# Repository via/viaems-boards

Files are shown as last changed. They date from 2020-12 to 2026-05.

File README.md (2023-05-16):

# viaems-boards
ViaEMS PCB Designs

In order of creation...
## Analog V1
 - Analog/ADC Core board based on a DIP TLC2543
 - All throughhole
 - Dedicated 5V supply
 - 4 Thermistor inputs
 - Inputs for EGO, BRV, MAP, TPS
 - 5 Spares

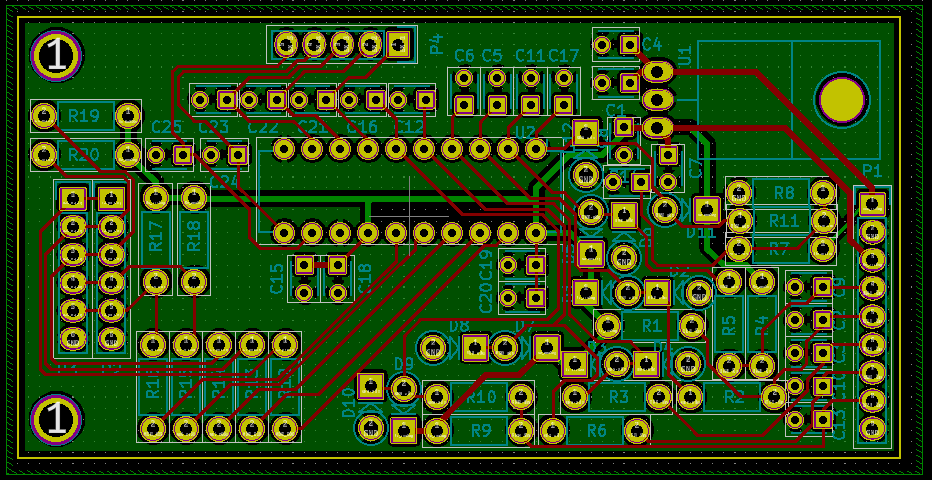
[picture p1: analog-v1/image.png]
 

## IO V1
 - IO core board
 - 4x ignition outputs
 - 6x Low side drivers
 - CAN driver
 - Digital inputs

Do not use because:
 - 3v supply for CAN doesn't work at all
 - the FETs without gate drivers has poor performance from a 3.3 V
   microcontroller
 - No VR inputs

## Viaems V1
Original all-in-one board for ViaEMS
 - STM32F407VGT
 - 8x Low side outputs (fed by gate drivers)
 - 4x ignition outputs
 - 2x High side drivers
 - Dedicated MAP and AAP sensors on-board
 - AD7888 SPI ADC with thermistor and core inputs, one spare
 - CAN driver

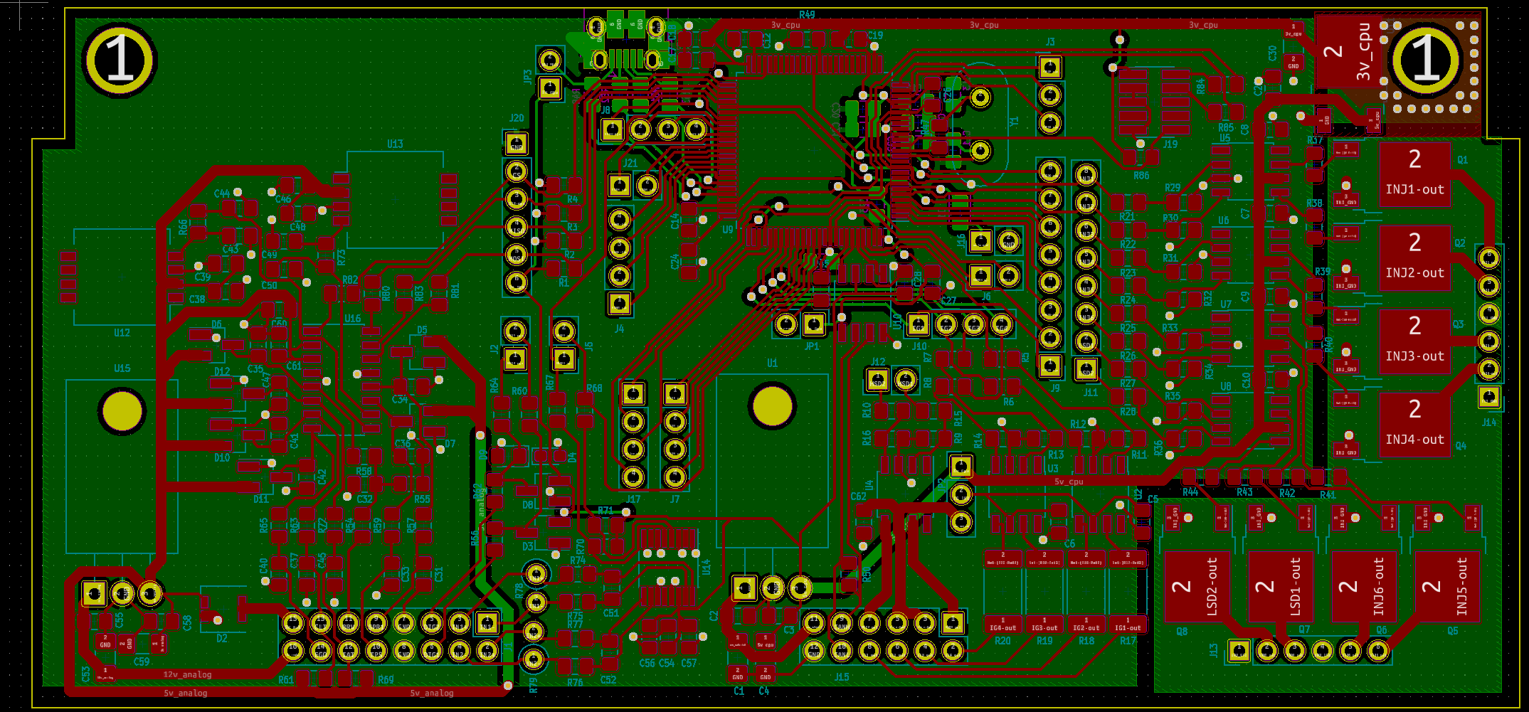
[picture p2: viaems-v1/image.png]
 

Shouldn't be used anymore, but really only because the outputs chosen for test
trigger vs real triggers are different in firmware.  The board can be used
again with some minor tweaks (and I have used this board for years)

## Analog V2
Experiment board to prototype use of the MAX11632, and some knock sensing
equipment.  The ADC samples fast enough to dedicate two inputs to knock sensing,
which uses an op amp input filter.  Provides core inputs, a dedicated MAP
sensor, and an additional 8 spare inputs.

The board works fine, but I'm unlikely to commit to the MAX11632: since it seems
incredibly finicky with SPI noise, and it doesn't provide a good way to know if
there is an issue. It requires a setup command.  The knock sensing filter works
great though.  Ultimately issues with this chip pushed me to investigate the
TLV2553.

Also, its way too big.

## IO V2
** Do not use! **
Simple breakout board as an upgrade to IO V2:
 - IO Core board
 - 5v supply (and fused output)
 - 4x ignition outputs
 - 8x Low Side drivers (including 4 injectors)
 - 2x Digital inputs
 - 2 VR inputs

Experiment with replacing the 2-port gate drivers with the 4-port MIC4469
 variant.  This board was made mostly to experiment with various FETs.

This board is missing inline resistors between the MIC4469 and FETs.  This is
incredibly important for the VND7NV04 -- without it, the negative pulse from
injectors destroys the gate control logic and causes it to latch partly on.

Ultimately this board is also *way* too big.

## Analog V3
Another experiment, this time for the TI TLV2553.  This ADC has only 11 inputs,
and samples at 200kHz (vs 300 kHz of the MAX11632).  However, its control is
identical to the TLC2543, which has self test functionality.  It is still fast
enough to allow for two inputs to be sampled at 40 kHz (and the rest at 10 kHz).
 - Analog Core board based on TLV2553
 - Small form factor (78x34 mm)
 - 2x SPI headers to make debugging easier
 - dedicated 5v supply (and fused output)
 - 1x MAP input
 - 2x knock sensor inputs
 - 3x Spare inputs

 I decided (after the fact) to make all the other boards the same form factor

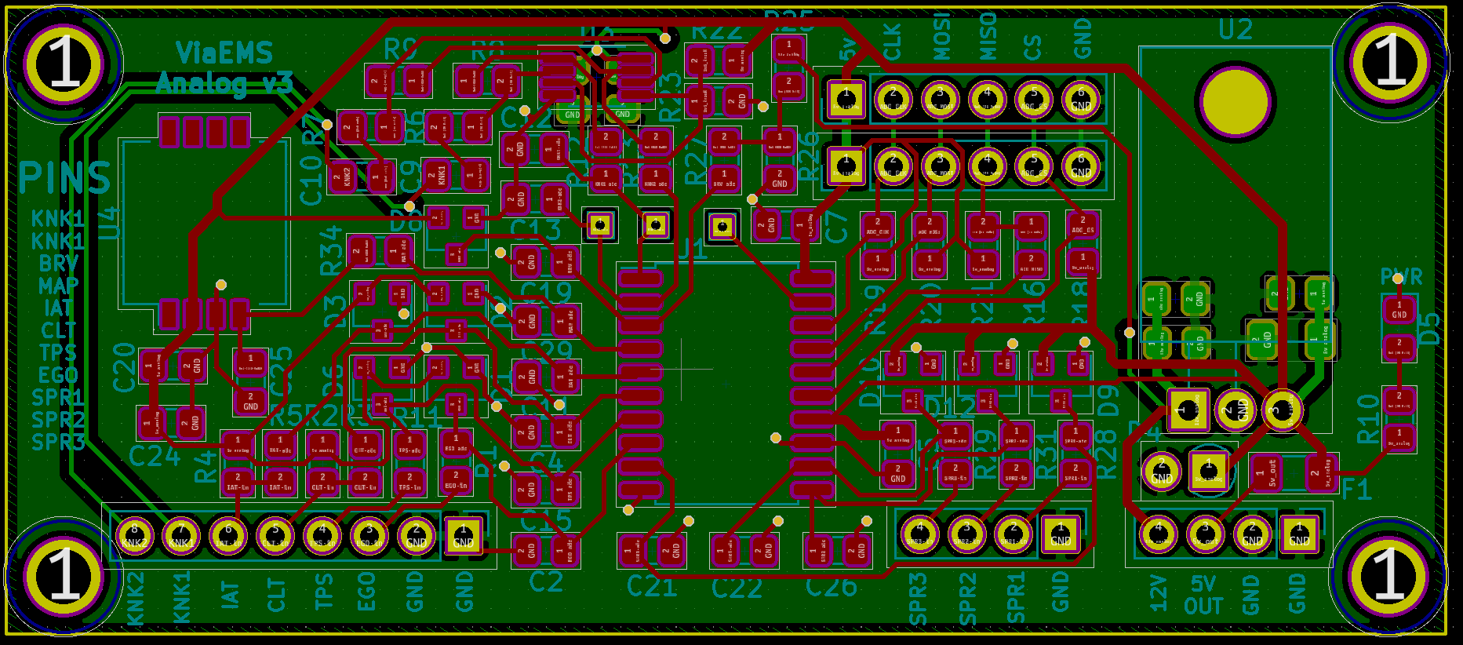
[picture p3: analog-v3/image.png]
 

## LSD V1 (Split from IO V2)
The full contents of IO V2 could not fit on a single 78x34 board, so it is split
into two -- one for the low side drivers, one for everything else.  Other
lessons learned from IO V2 were to add gate resistors for the FETs, and that
indicator LEDs are worth the effort to plan into the design.
 - Low side/Injector Core board
 - Small form factor (78x34)
 - 4x Injector outputs
 - 4x LSD outputs (or an extra 4x injectors)
 - Indicator LEDs

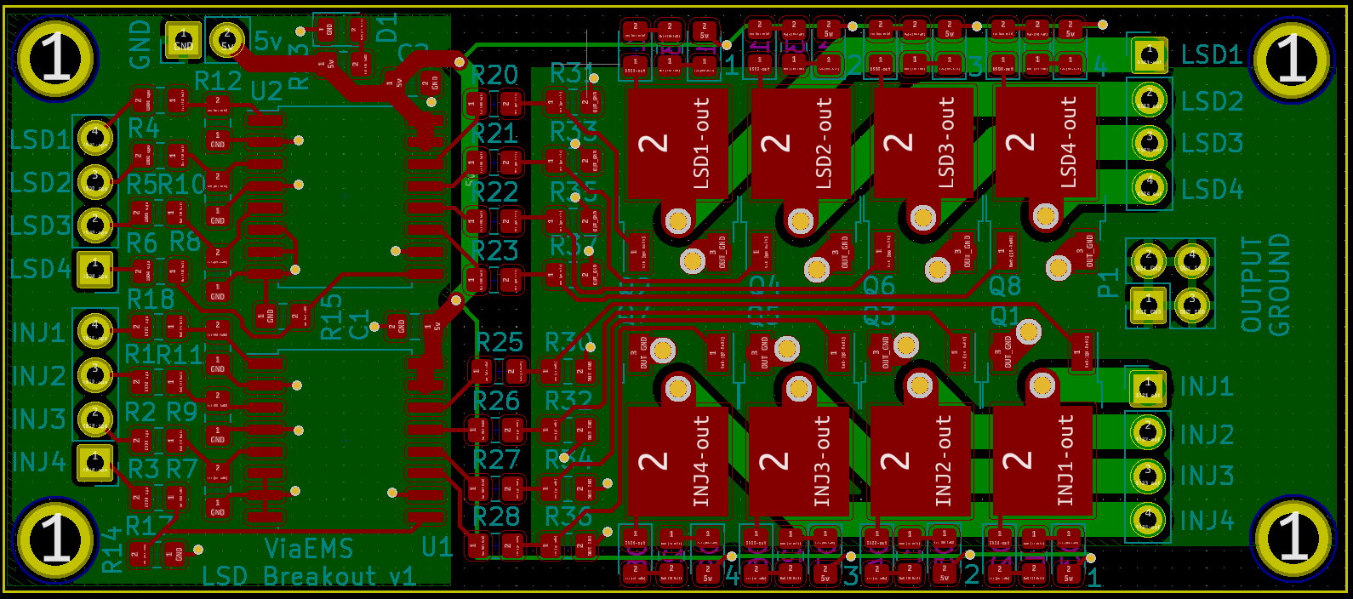
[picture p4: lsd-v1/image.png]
 

## Pwr-Ign-V1 (Split from IO V2)
An upgrade from IO V2, with gate resistors fixed, indicator LEDs on all outputs
and trigger inputs
 - 5v supply
 - 2x VR inputs
 - 2x Digital inputs
 - 4x Ignition outputs

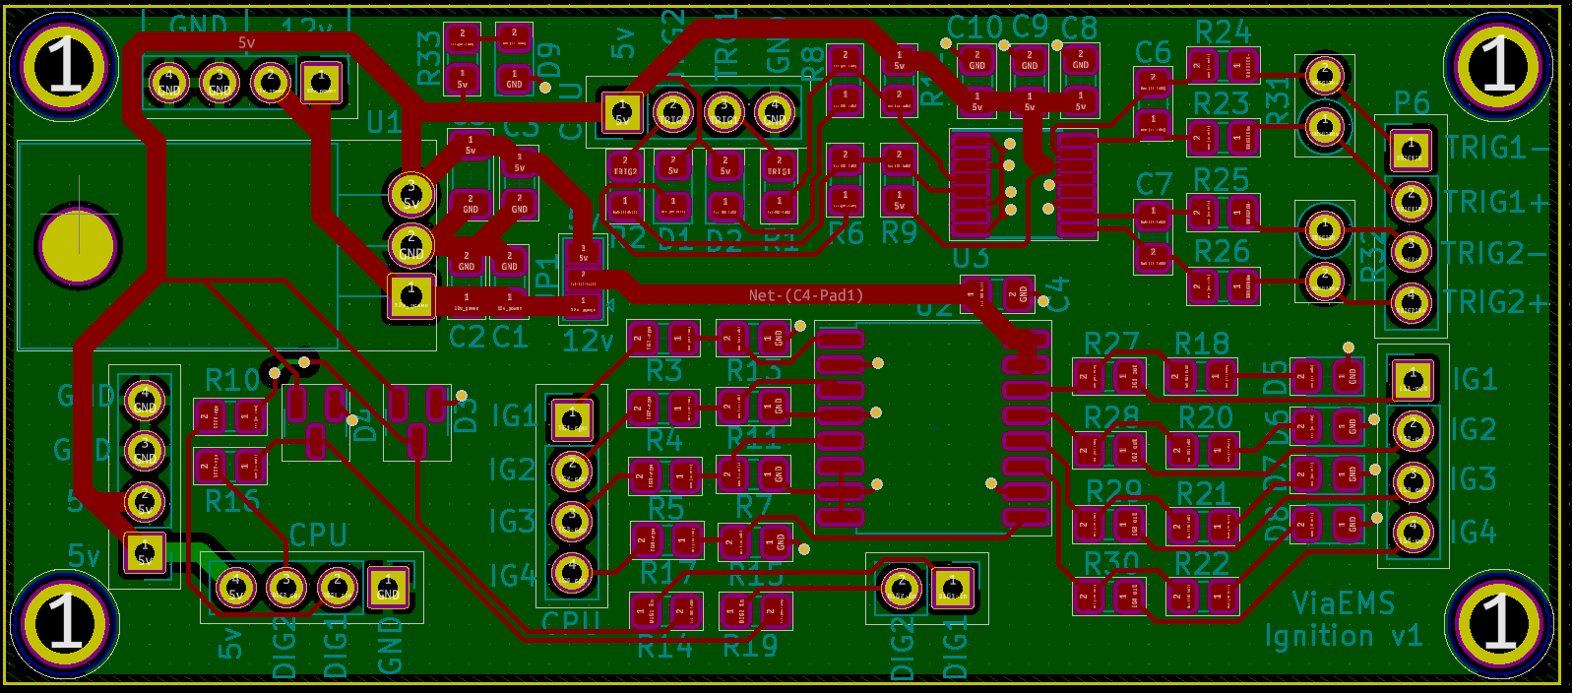
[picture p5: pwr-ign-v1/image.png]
 

## Proto-stm32f427 (v2)
Generic testing board for stm32f427 or gd32f470.  This is the same pcb
dimensions as the prior 3 boards, and comes with:
 - 100 LQFP footprint for microcontroller
 - USB Type-C (with FS-only pinout)
 - Optional soic-8 spi nor flash footprint on SPI1
 - Full 20 pin SWD+ETM trace connector

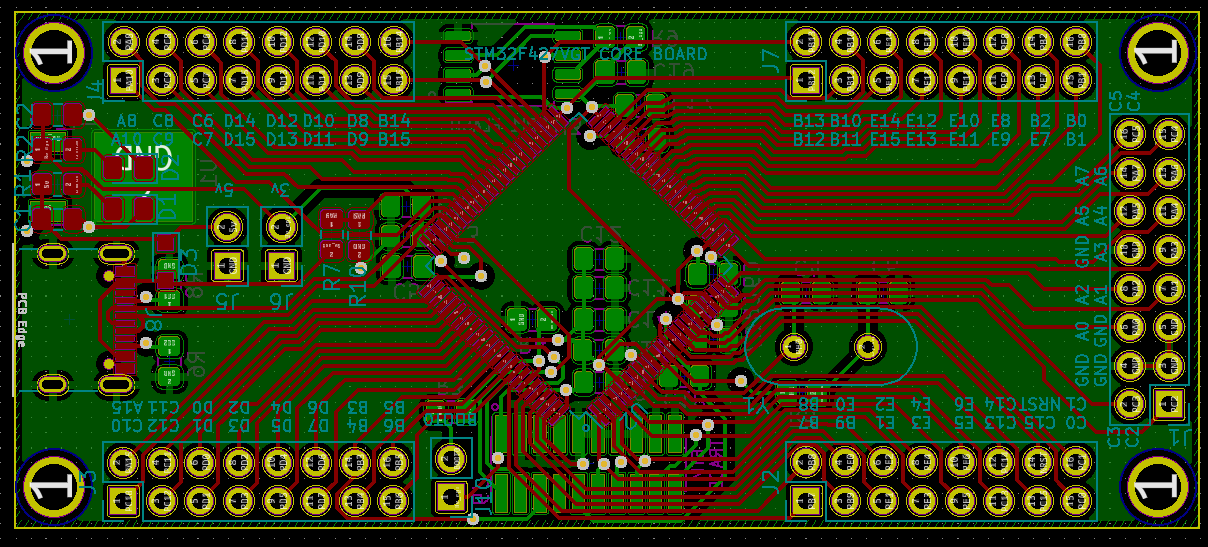
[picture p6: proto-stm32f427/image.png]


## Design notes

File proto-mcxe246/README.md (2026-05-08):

Power schemes:
 - USB Power -> 5v Vdd    (3.3v Reg powering uart)
 - USB Power -> 3v3 Vdd
 - SWD 3.3 V power -> 3v3 Vdd.  Uart?  Only if 5vusb jumpered.
 -

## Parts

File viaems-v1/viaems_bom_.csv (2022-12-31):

Component | Description | Part | References | Value | Footprint | Quantity Per PCB | Datasheet | Digikey-Part | Notes
1 | Unpolarized capacitor | C | C38 C46 C54 | 0.01 uF | C_0805_2012Metric_Pad1.15x1.40mm_HandSolder | 3 | ~ | 1276-1015-1-ND
2 | Unpolarized capacitor | C | C2 C3 C15 C18 C19 C20 C21 C22 C23 C24 C27 C28 C31 C32 C33 C37 C40 C45 C49 C55 C56 C58 C61 | 0.1 uF | C_0805_2012Metric_Pad1.15x1.40mm_HandSolder | 23 | ~ | 478-10836-1-ND | 35V
3 | Unpolarized capacitor | C | C43 | 0.1 uF | C_0805_2012Metric_Pad1.15x1.40mm_HandSolder | 1 | ~ | 1276-1015-1-ND
4 | Unpolarized capacitor | C | C44 C50 | 0.22 uF | C_0805_2012Metric_Pad1.15x1.40mm_HandSolder | 2 | ~ | 1276-1093-1-ND
5 | Unpolarized capacitor | C | C39 C48 | 0.33 uF | C_0805_2012Metric_Pad1.15x1.40mm_HandSolder | 2 | ~ | 1276-1123-1-ND
6 | Unpolarized capacitor | C | C34 C35 C36 C41 C42 C47 | 0.47 uF | C_0805_2012Metric_Pad1.15x1.40mm_HandSolder | 6 | ~ | 1276-6851-1-ND
7 | Unpolarized capacitor | C | C51 C52 | 1 nF | C_0805_2012Metric_Pad1.15x1.40mm_HandSolder | 2 | ~ | 399-1147-1-ND
8 | Unpolarized capacitor | C | C16 C26 C57 | 1 uF | C_0805_2012Metric_Pad1.15x1.40mm_HandSolder | 3 | ~ | 1276-1066-1-ND
9 | Unpolarized capacitor | C | C1 C53 | 10 uF | C_1206_3216Metric_Pad1.42x1.75mm_HandSolder | 2 | ~ | 445-8034-1-ND | 35V
10 | Unpolarized capacitor | C | C29 C60 | 10 uF | C_0805_2012Metric_Pad1.15x1.40mm_HandSolder | 2 | ~ | 587-3417-1-ND
11 | Unpolarized capacitor | C | C11 C13 | 16 pF | C_0805_2012Metric_Pad1.15x1.40mm_HandSolder | 2 | ~ | 311-4228-1-ND
12 | Unpolarized capacitor | C | C5 C6 C7 C8 C9 C10 C62 | 1uF | C_0805_2012Metric_Pad1.15x1.40mm_HandSolder | 7 | ~ | 1276-1029-1-ND | 35V
13 | Unpolarized capacitor | C | C12 C14 | 2.2 uF | C_0805_2012Metric_Pad1.15x1.40mm_HandSolder | 2 | ~ | 1276-1188-1-ND | ESR < 2.2 ohm ESR < 2.2 ohms
14 | Unpolarized capacitor | C | C17 | 4.7 uF | C_0805_2012Metric_Pad1.15x1.40mm_HandSolder | 1 | ~ | 445-14527-1-ND
15 | Unpolarized capacitor | C | C4 C30 C59 | 47 uF | C_1206_3216Metric_Pad1.42x1.75mm_HandSolder | 3 | ~ | 478-9009-1-ND | Tantalum 33 mOhm < ESR < 2.2 ohm
16 | Zener diode | D_Zener | D4 | 4.7 V | D_0603_1608Metric_Pad1.05x0.95mm_HandSolder | 1 | ~
17 | Zener diode | D_Zener | D9 | 4.7 V | D_0805_2012Metric_Pad1.15x1.40mm_HandSolder | 1 | ~
18 | schottky barrier diode | BAT54S | D3 D5 D6 D7 D8 D10 D11 D12 | BAT54S | SOT-23_Handsoldering | 8 | https://www.diodes.com/assets/Datasheets/ds11005.pdf | BAT54SLT1GOSCT-ND
19 | Diode | D | D1 | D | D_0805_2012Metric_Pad1.15x1.40mm_HandSolder | 1 | ~ | 478-7802-1-ND
20 | Polymer Protected Zener Diode, 5.6V, 1.15A, 24V, LS | ZEN056V115A24LS | D2 | ZEN056V115A24LS | Littelfuse_PolyZen-LS | 1 | http://m.littelfuse.com/~/media/electronics/datasheets/polyzen_devices/littelfuse_polyzen_standard_polyzen_catalog_datasheet.pdf.pdf | ZEN056V115A24LSCT-ND
21 | Generic connector, single row, 01x02, script generated (kicad-library-utils/schlib/autogen/connector/) | Conn_01x02 | J2 J5 J6 J12 J16 J21 | Conn_01x02 | PinHeader_1x02_P2.54mm_Vertical | 6 | ~ | 952-2262-ND
22 | Generic connector, single row, 01x03, script generated (kicad-library-utils/schlib/autogen/connector/) | Conn_01x03 | J3 | Conn_01x03 | PinHeader_1x03_P2.54mm_Vertical | 1 | ~ | 732-5316-ND
23 | Generic connector, single row, 01x04, script generated (kicad-library-utils/schlib/autogen/connector/) | Conn_01x04 | J4 J7 J8 J10 J17 | Conn_01x04 | PinHeader_1x04_P2.54mm_Vertical | 5 | ~ | 732-5317-ND
24 | Generic connector, single row, 01x06, script generated (kicad-library-utils/schlib/autogen/connector/) | Conn_01x06 | J13 J14 J20 | Conn_01x06 | PinHeader_1x06_P2.54mm_Vertical | 3 | ~ | 732-5319-ND
25 | Generic connector, single row, 01x08, script generated (kicad-library-utils/schlib/autogen/connector/) | Conn_01x08 | J9 J11 | Conn_01x08 | PinHeader_1x08_P2.54mm_Vertical | 2 | ~ | 732-5321-ND
26 | Generic connector, double row, 02x06, odd/even pin numbering scheme (row 1 odd numbers, row 2 even numbers), script generated (kicad-library-utils/schlib/autogen/connector/) | Conn_02x06_Odd_Even | J15 | Conn_02x06_Odd_Even | PinHeader_2x06_P2.54mm_Vertical | 1 | ~ | 732-5297-ND
27 | Generic connector, double row, 02x08, counter clockwise pin numbering scheme (similar to DIP packge numbering), script generated (kicad-library-utils/schlib/autogen/connector/) | Conn_02x08_Counter_Clockwise | J1 | Conn_02x08_Counter_Clockwise | PinHeader_2x08_P2.54mm_Vertical | 1 | ~ | 609-3220-ND
28 | Cortex Debug Connector, standard ARM Cortex-M SWD and JTAG interface | Conn_ARM_JTAG_SWD_10 | J19 | Conn_ARM_JTAG_SWD_10 | PinHeader_2x05_P1.27mm_Vertical_SMD | 1 | http://infocenter.arm.com/help/topic/com.arm.doc.faqs/attached/13634/cortex_debug_connectors.pdf | SAM9438-ND
29 | USB Micro Type B connector | USB_B_Micro | J18 | USB_B_Micro | USB_Micro-B_Amphenol_10103594-0001LF_Horizontal | 1 | ~ | 609-4050-1-ND
30 | Jumper, normally closed | Jumper | JP1 JP3 | Jumper | PinHeader_1x02_P2.54mm_Vertical | 2 | ~ | 952-2262-ND
31 | Dual jumper, normally closed | Jumper_NC_Dual | JP2 | Jumper_NC_Dual | PinHeader_1x03_P2.54mm_Vertical | 1 | ~ | 732-5316-ND
32 | N-MOSFET transistor, gate/drain/source | Q_NMOS_GDS | Q1 Q2 Q3 Q4 Q5 Q6 Q7 Q8 | VND7NV04 | TO-252-2 | 8 | ~ | 497-11707-1-ND
33 | Resistor | R | R1 R2 R3 R4 R11 R12 R13 R14 R15 R16 R29 R30 R31 R32 R33 R34 R35 R36 R46 R49 R86 | 100k | R_0805_2012Metric_Pad1.15x1.40mm_HandSolder | 21 | ~ | P100KDACT-ND
34 | Resistor | R | R70 R71 | 10k | R_0805_2012Metric_Pad1.15x1.40mm_HandSolder | 2 | ~ | RNCF0805DTE10K0CT-ND
35 | Resistor | R | R50 | 120 | R_0805_2012Metric_Pad1.15x1.40mm_HandSolder | 1 | ~ | P16874CT-ND
36 | Resistor | R | R17 R18 R19 R20 | 150 | R_2512_6332Metric_Pad1.52x3.35mm_HandSolder | 4 | ~ | 541-150XCT-ND | 1W
37 | Resistor | R | R37 R38 R39 R40 R41 R42 R43 R44 | 150 | R_0805_2012Metric_Pad1.15x1.40mm_HandSolder | 8 | ~ | RNCP0805FTD150RCT-ND
38 | Resistor | R | R5 R6 R7 R8 R9 R10 R21 R22 R23 R24 R25 R26 R27 R28 R45 R48 R53 R56 R60 R62 R64 R66 R67 R68 R73 R74 R75 R76 R77 | 1k | R_0805_2012Metric_Pad1.15x1.40mm_HandSolder | 29 | ~ | RNCP0805FTD1K00CT-ND
39 | Resistor | R | R55 | 1k | R_0805_2012Metric_Pad1.15x1.40mm_HandSolder | 1 | ~ | P1.0KDACT-ND | 0.1%
40 | Resistor | R | R78 R79 | 1k | R_Axial_DIN0207_L6.3mm_D2.5mm_P2.54mm_Vertical | 2 | ~ | PPC1.0KW-1CT-ND | 1W
41 | Resistor | R | R61 R69 | 2.4k | R_0805_2012Metric_Pad1.15x1.40mm_HandSolder | 2 | ~ | P2.4KDACT-ND
42 | Resistor | R | R51 R52 | 22 | R_0805_2012Metric_Pad1.15x1.40mm_HandSolder | 2 | ~ | A130124CT-ND
43 | Resistor | R | R47 R80 R81 R82 R83 R84 R85 | 220 | R_0805_2012Metric_Pad1.15x1.40mm_HandSolder | 7 | ~ | A129741CT-ND
44 | Resistor | R | R54 | 3.9k | R_0805_2012Metric_Pad1.15x1.40mm_HandSolder | 1 | ~ | P3.9KDACT-ND | 0.1%
45 | Resistor | R | R57 R58 R59 R63 R65 R72 | 470 | R_0805_2012Metric_Pad1.15x1.40mm_HandSolder | 6 | ~ | 311-470CRCT-ND
46 |  | AD7888 | U16 | AD7888 | SOIC-16_3.9x9.9mm_P1.27mm | 1 |  | AD7888ARZ-REEL7CT-ND
47 |  | LM2940 | U1 U15 | LM2940 | TO-220-3_Horizontal_TabDown | 2 |  | LM2940T-5.0/NOPB-ND
48 |  | MAX9926UAEE+ | U14 | MAX9926UAEE+ | QSOP-16_3.9x4.9mm_P0.635mm | 1 |  | MAX9926UAEE+TCT-ND
49 | High-Speed CAN Transceiver, 1Mbps, 5V supply, Vio pin, -40C to +150C, SOIC8 package | MCP2562-H-SN | U10 | MCP2562-H-SN | SOIC-8_3.9x4.9mm_P1.27mm | 1 | http://ww1.microchip.com/downloads/en/DeviceDoc/25167A.pdf | MCP2562-H/SN
50 | Absolute pressure sensor, 15 to 115kPa, analog output, integrated signal conditioning, temperature compensated, SO package | MPXA6115A | U13 | MPXH6115AC6U | Freescale_98ARH99089A | 1 | http://www.nxp.com/files/sensors/doc/data_sheet/MPXA6115A.pdf | MPXH6115AC6U-ND
51 | Absolute pressure sensor, 15 to 115kPa, analog output, integrated signal conditioning, temperature compensated, SO package | MPXA6115A | U12 | MPXH6400A | Freescale_98ARH99089A | 1 | http://www.nxp.com/files/sensors/doc/data_sheet/MPXA6115A.pdf | MPXH6400AC6T1CT-ND
52 | 1A Low drop-out regulator, Fixed Output 3.3V, TO-252 (DPAK) | NCP1117-3.3_TO252 | U11 | NCP1117-3.3_TO252 | TO-252-2 | 1 | http://www.onsemi.com/pub_link/Collateral/NCP1117-D.PDF | NCP1117DT33T5GOSCT-ND
53 | ARM Cortex-M4 MCU, 1024KB flash, 128KB RAM, 168MHz, 1.8-3.6V, 82 GPIO, LQFP-100 | STM32F407VGTx | U9 | STM32F407VGTx | LQFP-100_14x14mm_P0.5mm | 1 | http://www.st.com/st-web-ui/static/active/en/resource/technical/document/datasheet/DM00037051.pdf | 497-17438-ND
54 |  | TC442xA | U2 U3 U4 U5 U6 U7 U8 | TC442xA | SOIC-8_3.9x4.9mm_P1.27mm | 7 |  | TC4427EOA713CT-ND
55 | Two pin crystal | Crystal | Y1 | 8 Mhz | Crystal_HC49-U_Vertical | 1 | ~ | 535-10212-1-ND
Component Groups: | 55
Component Count: | 208
Fitted Components: | 208
Number of PCBs: | 1
Total components: | 208
Schematic Version:
Schematic Date:
BoM Date: | Sun 05 May 2019 05:27:50 PM EDT
Schematic Source: | /home/via/dev/tfi-board/viaems/viaems.sch
KiCad Version: | Eeschema 5.0.2+dfsg1-1

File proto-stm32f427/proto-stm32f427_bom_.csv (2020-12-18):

Component | Description | Part | References | Value | Footprint | Quantity Per PCB | Datasheet | Digikey-Part
1 | Unpolarized capacitor | C | C8 C10 C11 C12 C13 C14 C15 C16 C18 | 0.1 uF | C_0805_2012Metric_Pad1.15x1.40mm_HandSolder | 9 | ~ | 478-10836-1-ND
2 | Unpolarized capacitor | C | C7 C17 | 1 uF | C_0805_2012Metric_Pad1.15x1.40mm_HandSolder | 2 | ~ | 1276-1066-1-ND
3 | Unpolarized capacitor | C | C1 | 10 uF | C_0805_2012Metric_Pad1.15x1.40mm_HandSolder | 1 | ~ | 587-3417-1-ND
4 | Unpolarized capacitor | C | C3 C5 | 16 pF | C_0805_2012Metric_Pad1.15x1.40mm_HandSolder | 2 | ~ | 311-4228-1-ND
5 | Unpolarized capacitor | C | C4 C6 | 2.2 uF | C_0805_2012Metric_Pad1.15x1.40mm_HandSolder | 2 | ~ | 1276-1188-1-ND
6 | Unpolarized capacitor | C | C9 | 4.7 uF | C_0805_2012Metric_Pad1.15x1.40mm_HandSolder | 1 | ~ | 445-14527-1-ND
7 | Unpolarized capacitor | C | C2 | 47 uF | C_0805_2012Metric_Pad1.15x1.40mm_HandSolder | 1 | ~ | 718-1608-1-ND
8 | 40V 0.35A Small Signal Schottky Diode, SOD-323 | BAT48JFILM | D1 | BAT48JFILM | D_SOD-323_HandSoldering | 1 | www.st.com/resource/en/datasheet/bat48.pdf | B0530WS-FDICT-ND
9 | Light emitting diode | LED | D2 D3 | LED | LED_0805_2012Metric_Pad1.15x1.40mm_HandSolder | 2 | ~ | 475-1415-1-ND
10 | Cortex Debug Connector, standard ARM Cortex-M SWD and JTAG interface | Conn_ARM_JTAG_SWD_10 | J4 | Debug | PinHeader_2x05_P1.27mm_Vertical_SMD | 1 | http://infocenter.arm.com/help/topic/com.arm.doc.faqs/attached/13634/cortex_debug_connectors.pdf | SAM9438-ND
11 | Generic connector, double row, 02x25, odd/even pin numbering scheme (row 1 odd numbers, row 2 even numbers), script generated (kicad-library-utils/schlib/autogen/connector/) | Conn_02x25_Odd_Even | J1 J5 | Left | PinHeader_2x25_P2.54mm_Vertical | 2 | ~ | HTSW-125-14-T-D-ND
12 | Micro SD Card Socket | Micro_SD_Card | J2 | Micro_SD_Card | microSD_HC_Wuerth_693072010801 | 1 | http://katalog.we-online.de/em/datasheet/693072010801.pdf | 732-3820-1-ND
13 | USB Micro Type B connector | USB_B_Micro | J3 | USB | USB_Micro-B_Amphenol_10103594-0001LF_Horizontal | 1 | ~ | 609-4050-1-ND
14 | Jumper, normally closed | Jumper | JP1 | Idd | PinHeader_1x02_P2.54mm_Vertical | 1 | ~ | 952-2262-ND
15 | Resistor | R | R2 | 100k | R_0805_2012Metric_Pad1.15x1.40mm_HandSolder | 1 | ~ | P100KDACT-ND
16 | Resistor | R | R5 | 10k | R_0805_2012Metric_Pad1.15x1.40mm_HandSolder | 1 | ~ | RNCF0805DTE10K0CT-ND
17 | Resistor | R | R1 | 1k | R_0805_2012Metric_Pad1.15x1.40mm_HandSolder | 1 | ~ | RNCP0805FTD1K00CT-ND
18 | Resistor | R | R3 R6 R7 | 220 | R_0805_2012Metric_Pad1.15x1.40mm_HandSolder | 3 | ~ | A129741CT-ND
19 | Resistor | R | R4 | 4.7k | R_0805_2012Metric_Pad1.15x1.40mm_HandSolder | 1 | ~ | 311-4.70KCRCT-ND
20 | 500-mA Low Dropout Regulator, TO-220 | LM2937xT | U1 | NCV5501 | TO-252-2 | 1 | https://www.onsemi.com/pub/Collateral/NCP5500-D.PDF | NCV5501DT33GOS-ND
21 | ARM Cortex-M4 MCU, 1024KB flash, 192KB RAM, 180MHz, 1.8-3.6V, 82 GPIO, LQFP-100 | STM32F427VGTx | U2 | STM32F427VGTx | LQFP-100_14x14mm_P0.5mm | 1 | http://www.st.com/st-web-ui/static/active/en/resource/technical/document/datasheet/DM00071990.pdf | 497-16769-ND
22 | Two pin crystal | Crystal | Y1 | 8 MHz | Crystal_HC49-U_Vertical | 1 | ~ | 535-10212-1-ND
Component Groups: | 22
Component Count: | 37
Fitted Components: | 37
Number of PCBs: | 1
Total components: | 37
Schematic Version:
Schematic Date:
BoM Date: | Sun 12 Apr 2020 11:54:07 PM EDT
Schematic Source: | /home/via/dev/proto-stm32f427/proto-stm32f427.sch
KiCad Version: | Eeschema 5.0.2+dfsg1-1

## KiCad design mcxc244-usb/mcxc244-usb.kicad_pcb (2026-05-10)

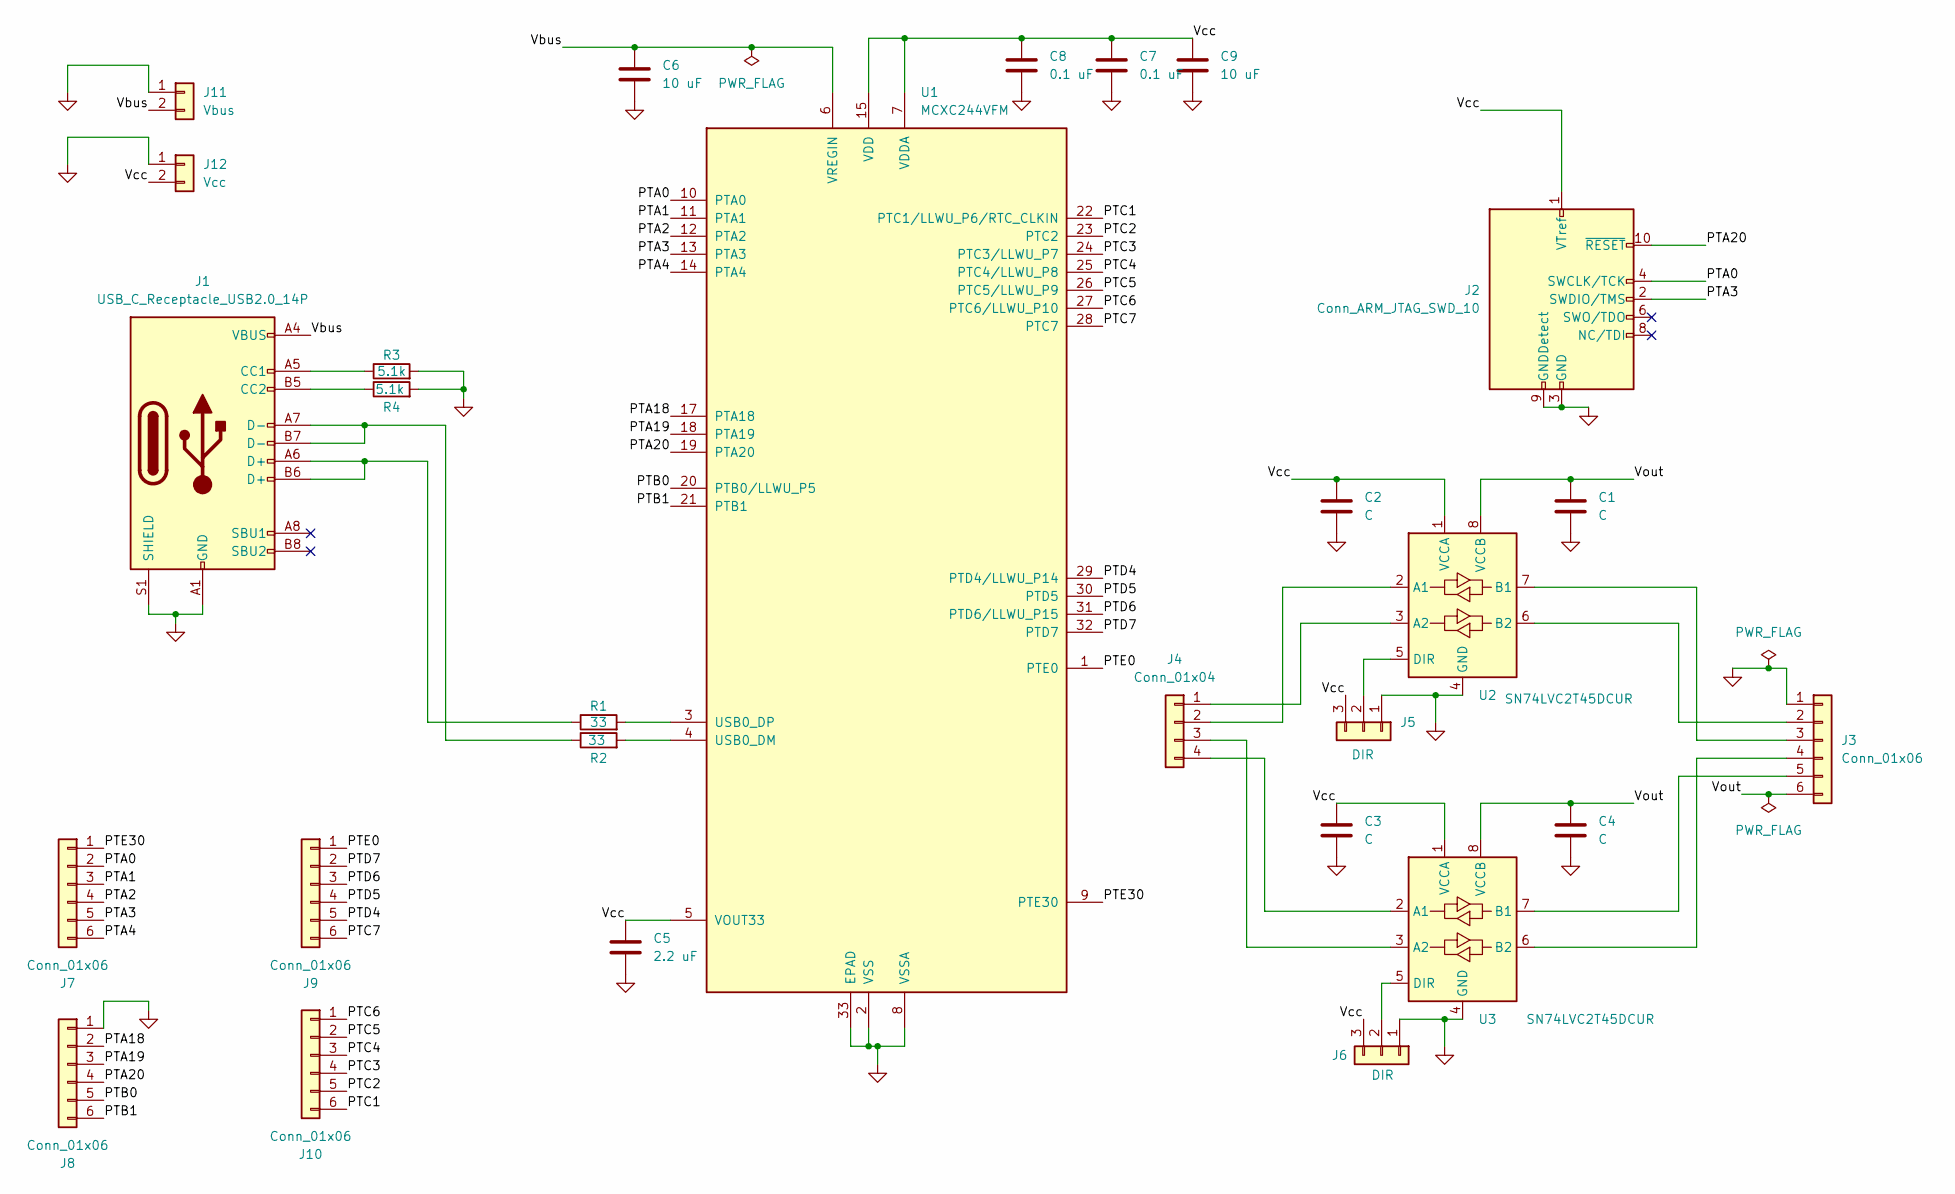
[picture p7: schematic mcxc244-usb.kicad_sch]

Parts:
C1, C2, C3, C4: C; C_0805_2012Metric
C5: 2.2 uF; C_0805_2012Metric
C6, C9: 10 uF; C_0805_2012Metric
C7, C8: 0.1 uF; C_0805_2012Metric
J1: USB_C_Receptacle_USB2.0_14P; USB_C_Receptacle_GCT_USB4105-xx-A_16P_TopMnt_Horizontal
J2: Conn_ARM_JTAG_SWD_10; PinHeader_2x05_P1.27mm_Vertical_SMD
J3, J7, J8, J9, J10: Conn_01x06; PinHeader_1x06_P2.54mm_Vertical
J4: Conn_01x04; PinHeader_1x04_P2.54mm_Vertical
J5, J6: DIR; PinHeader_1x03_P2.54mm_Vertical
J11: Vbus; PinHeader_1x02_P2.54mm_Vertical
J12: Vcc; PinHeader_1x02_P2.54mm_Vertical
R1, R2: 33; R_0805_2012Metric
R3, R4: 5.1k; R_0805_2012Metric
U1: MCXC244VFM; QFN-32-1EP_5x5mm_P0.5mm_EP3.45x3.45mm
U2, U3: SN74LVC2T45DCUR; VSSOP-8_2.3x2mm_P0.5mm

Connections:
/PTA0: J2.4 (SWCLK/TCK), J7.2, U1.10 (PTA0)
/PTA1: J7.3, U1.11 (PTA1)
/PTA2: J7.4, U1.12 (PTA2)
/PTA3: J2.2 (SWDIO/TMS), J7.5, U1.13 (PTA3)
/PTA4: J7.6, U1.14 (PTA4)
/PTA18: J8.2, U1.17 (PTA18)
/PTA19: J8.3, U1.18 (PTA19)
/PTA20: J2.10 (~RESET), J8.4, U1.19 (PTA20)
/PTB0: J8.5, U1.20 (PTB0/LLWU_P5)
/PTB1: J8.6, U1.21 (PTB1)
/PTC1: J10.6, U1.22 (PTC1/LLWU_P6/RTC_CLKIN)
/PTC2: J10.5, U1.23 (PTC2)
/PTC3: J10.4, U1.24 (PTC3/LLWU_P7)
/PTC4: J10.3, U1.25 (PTC4/LLWU_P8)
/PTC5: J10.2, U1.26 (PTC5/LLWU_P9)
/PTC6: J10.1, U1.27 (PTC6/LLWU_P10)
/PTC7: J9.6, U1.28 (PTC7)
/PTD4: J9.5, U1.29 (PTD4/LLWU_P14)
/PTD5: J9.4, U1.30 (PTD5)
/PTD6: J9.3, U1.31 (PTD6/LLWU_P15)
/PTD7: J9.2, U1.32 (PTD7)
/PTE0: J9.1, U1.1 (PTE0)
/PTE30: J7.1, U1.9 (PTE30)
/Vbus: C6.1, J1.A4 (VBUS), J1.A9 (VBUS), J1.B4 (VBUS), J1.B9 (VBUS), J11.2, U1.6 (VREGIN)
/Vcc: C2.1, C3.1, C5.1, C7.1, C8.1, C9.1, J2.1 (VTref), J5.3, J6.3, J12.2, U1.5 (VOUT33), U1.7 (VDDA), U1.15 (VDD), U2.1 (VCCA), U3.1 (VCCA)
/Vout: C1.1, C4.1, J3.6, U2.8 (VCCB), U3.8 (VCCB)
GND: C1.2, C2.2, C3.2, C4.2, C5.2, C6.2, C7.2, C8.2, C9.2, J1.A1 (GND), J1.A12 (GND), J1.B1 (GND), J1.B12 (GND), J1.S1 (SHIELD), J2.3 (GND), J2.5 (GND), J2.9 (GNDDetect), J3.1, J5.1, J6.1, J8.1, J11.1, J12.1, R3.2, R4.2, U1.2 (VSS), U1.8 (VSSA), U1.16 (VSS), U1.33 (EPAD), U2.4 (GND), U3.4 (GND)
unnamed: J1.A5 (CC1), R3.1
unnamed: J1.B5 (CC2), R4.1
unnamed: J1.A6 (D+), J1.B6 (D+), R1.1
unnamed: J1.A7 (D-), J1.B7 (D-), R2.1
unnamed: J3.2, U2.6 (B2)
unnamed: J3.3, U2.7 (B1)
unnamed: J3.4, U3.6 (B2)
unnamed: J3.5, U3.7 (B1)
unnamed: J4.1, U2.3 (A2)
unnamed: J4.2, U2.2 (A1)
unnamed: J4.3, U3.3 (A2)
unnamed: J4.4, U3.2 (A1)
unnamed: J5.2, U2.5 (DIR)
unnamed: J6.2, U3.5 (DIR)
unnamed: R2.2, U1.4 (USB0_DM)
unnamed: R1.2, U1.3 (USB0_DP)

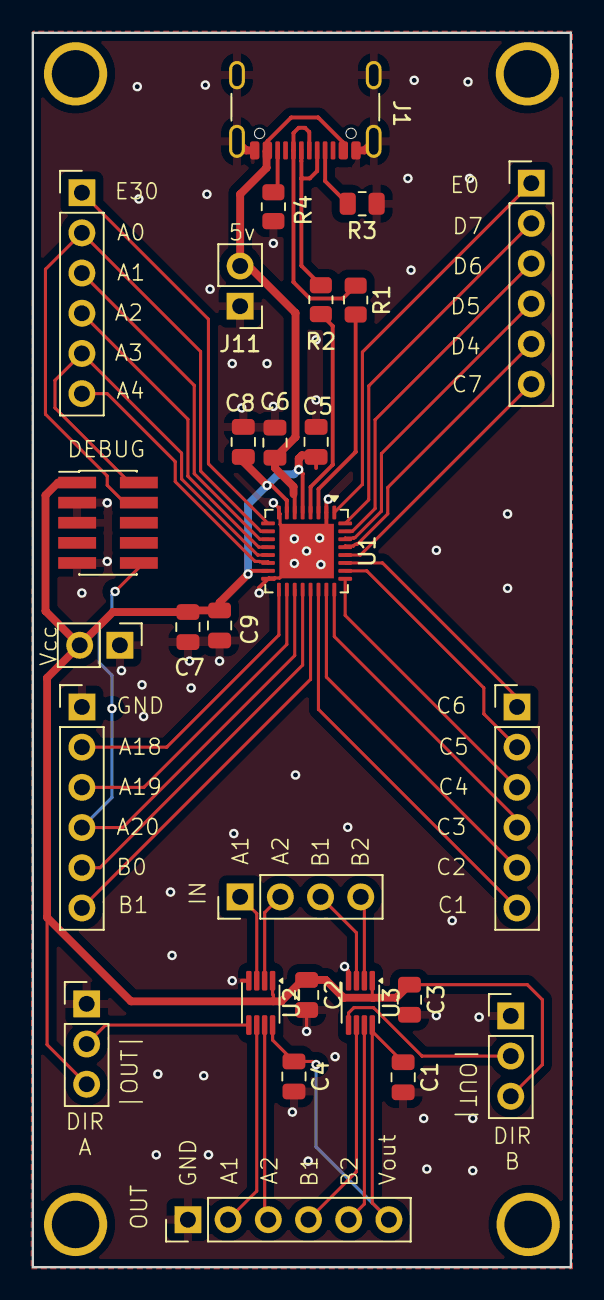
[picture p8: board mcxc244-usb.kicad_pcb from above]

Board: 2 copper layers, 34.0 x 78.0 mm, 28 parts (0 on the bottom side), 43 nets.

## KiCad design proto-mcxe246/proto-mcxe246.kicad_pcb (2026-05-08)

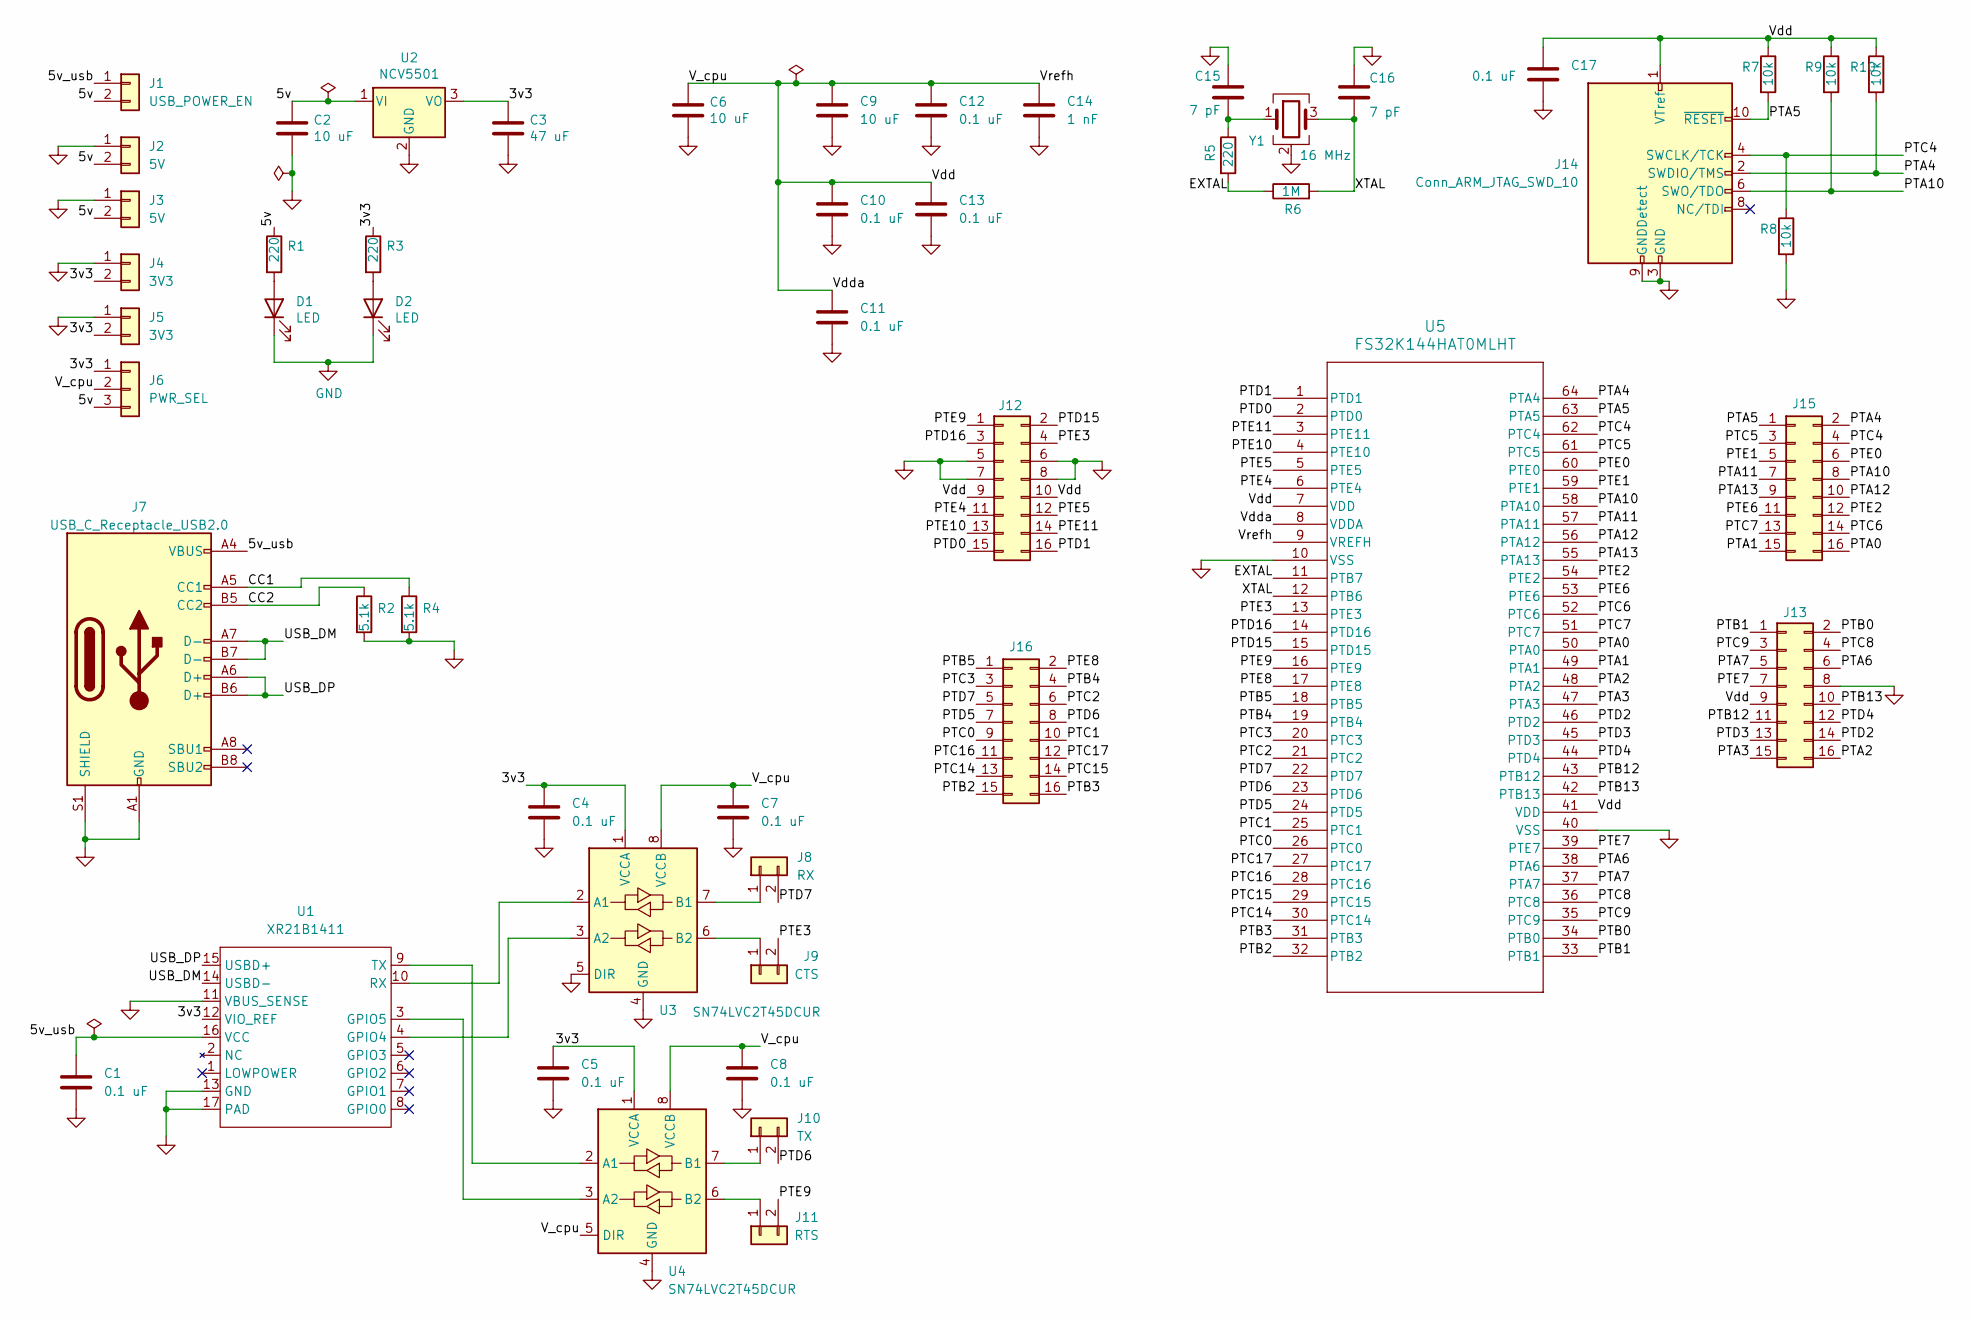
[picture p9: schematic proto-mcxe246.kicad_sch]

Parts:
C1, C4, C5, C7, C8, C10, C11, C12, C13, C17: 0.1 uF; C_0805_2012Metric_Pad1.18x1.45mm_HandSolder
C2: 10 uF; C_0805_2012Metric_Pad1.18x1.45mm_HandSolder; Digikey-Part 587-3417-1-ND
C3: 47 uF; C_0805_2012Metric_Pad1.18x1.45mm_HandSolder; Digikey-Part 718-1608-1-ND
C6: 10 uF; C_0805_2012Metric_Pad1.18x1.45mm_HandSolder; Digikey-Part 718-1608-1-ND
C9: 10 uF; C_0805_2012Metric_Pad1.18x1.45mm_HandSolder
C14: 1 nF; C_0805_2012Metric_Pad1.18x1.45mm_HandSolder
C15, C16: 7 pF; C_0805_2012Metric_Pad1.18x1.45mm_HandSolder
D1, D2: LED; LED_0805_2012Metric_Pad1.15x1.40mm_HandSolder; Digikey-Part 475-1415-1-ND
J1: USB_POWER_EN; PinHeader_1x02_P2.54mm_Vertical
J2, J3: 5V; PinHeader_1x02_P2.54mm_Vertical
J4, J5: 3V3; PinHeader_1x02_P2.54mm_Vertical
J6: PWR_SEL; PinHeader_1x03_P2.54mm_Vertical
J7: USB_C_Receptacle_USB2.0; USB_C_Receptacle_GCT_USB4105-xx-A_16P_TopMnt_Horizontal; Digikey-Part 2073-USB4105-GF-ACT-ND
J8: RX; PinHeader_1x02_P2.54mm_Vertical
J9: CTS; PinHeader_1x02_P2.54mm_Vertical
J10: TX; PinHeader_1x02_P2.54mm_Vertical
J11: RTS; PinHeader_1x02_P2.54mm_Vertical
J12, J13, J15, J16: Conn_02x08_Odd_Even; PinHeader_2x08_P2.54mm_Vertical
J14: Conn_ARM_JTAG_SWD_10; PinHeader_2x05_P1.27mm_Vertical_SMD
R1, R3: 220; R_0805_2012Metric_Pad1.20x1.40mm_HandSolder; Digikey-Part A129741CT-ND
R2, R4: 5.1k; R_0805_2012Metric_Pad1.20x1.40mm_HandSolder
R5: 220; R_0805_2012Metric_Pad1.20x1.40mm_HandSolder
R6: 1M; R_0805_2012Metric_Pad1.20x1.40mm_HandSolder
R7, R8, R9, R10: 10k; R_0805_2012Metric_Pad1.20x1.40mm_HandSolder
U1: XR21B1411; QFN-16-1EP_3x3mm_P0.5mm_EP1.7x1.7mm
U2: NCV5501; TO-252-2; Digikey-Part NCV5501DT33GOS-ND
U3, U4: SN74LVC2T45DCUR; VSSOP-8_2.3x2mm_P0.5mm
U5: FS32K144HAT0MLHT; SOT1699-1_LQFP64_NXP
Y1: 16 MHz; Crystal_SMD_2520-4Pin_2.5x2.0mm; Digikey-Part 535-13361-1-ND -

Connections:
/3v3: C3.1, C4.1, C5.1, J4.2, J5.2, J6.1, R3.1, U1.12 (VIO_REF), U2.3 (VO), U3.1 (VCCA), U4.1 (VCCA)
/5v: C2.1, J1.2, J2.2, J3.2, J6.3, R1.1, U2.1 (VI)
/5v_usb: C1.1, J1.1, J7.A4 (VBUS), J7.A9 (VBUS), J7.B4 (VBUS), J7.B9 (VBUS), U1.16 (VCC)
/CC1: J7.A5 (CC1), R4.1
/CC2: J7.B5 (CC2), R2.1
/EXTAL: R5.2, R6.1, U5.11 (PTB7)
/PTA0: J15.16, U5.50 (PTA0)
/PTA1: J15.15, U5.49 (PTA1)
/PTA2: J13.16, U5.48 (PTA2)
/PTA3: J13.15, U5.47 (PTA3)
/PTA4: J14.2 (SWDIO/TMS), J15.2, R10.2, U5.64 (PTA4)
/PTA5: J14.10 (~RESET), J15.1, R7.2, U5.63 (PTA5)
/PTA6: J13.6, U5.38 (PTA6)
/PTA7: J13.5, U5.37 (PTA7)
/PTA10: J14.6 (SWO/TDO), J15.8, R9.2, U5.58 (PTA10)
/PTA11: J15.7, U5.57 (PTA11)
/PTA12: J15.10, U5.56 (PTA12)
/PTA13: J15.9, U5.55 (PTA13)
/PTB0: J13.2, U5.34 (PTB0)
/PTB1: J13.1, U5.33 (PTB1)
/PTB2: J16.15, U5.32 (PTB2)
/PTB3: J16.16, U5.31 (PTB3)
/PTB4: J16.4, U5.19 (PTB4)
/PTB5: J16.1, U5.18 (PTB5)
/PTB12: J13.11, U5.43 (PTB12)
/PTB13: J13.10, U5.42 (PTB13)
/PTC0: J16.9, U5.26 (PTC0)
/PTC1: J16.10, U5.25 (PTC1)
/PTC2: J16.6, U5.21 (PTC2)
/PTC3: J16.3, U5.20 (PTC3)
/PTC4: J14.4 (SWCLK/TCK), J15.4, R8.1, U5.62 (PTC4)
/PTC5: J15.3, U5.61 (PTC5)
/PTC6: J15.14, U5.52 (PTC6)
/PTC7: J15.13, U5.51 (PTC7)
/PTC8: J13.4, U5.36 (PTC8)
/PTC9: J13.3, U5.35 (PTC9)
/PTC14: J16.13, U5.30 (PTC14)
/PTC15: J16.14, U5.29 (PTC15)
/PTC16: J16.11, U5.28 (PTC16)
/PTC17: J16.12, U5.27 (PTC17)
/PTD0: J12.15, U5.2 (PTD0)
/PTD1: J12.16, U5.1 (PTD1)
/PTD2: J13.14, U5.46 (PTD2)
/PTD3: J13.13, U5.45 (PTD3)
/PTD4: J13.12, U5.44 (PTD4)
/PTD5: J16.7, U5.24 (PTD5)
/PTD6: J10.2, J16.8, U5.23 (PTD6)
/PTD7: J8.2, J16.5, U5.22 (PTD7)
/PTD15: J12.2, U5.15 (PTD15)
/PTD16: J12.3, U5.14 (PTD16)
/PTE0: J15.6, U5.60 (PTE0)
/PTE1: J15.5, U5.59 (PTE1)
/PTE2: J15.12, U5.54 (PTE2)
/PTE3: J9.2, J12.4, U5.13 (PTE3)
/PTE4: J12.11, U5.6 (PTE4)
/PTE5: J12.12, U5.5 (PTE5)
/PTE6: J15.11, U5.53 (PTE6)
/PTE7: J13.7, U5.39 (PTE7)
/PTE8: J16.2, U5.17 (PTE8)
/PTE9: J11.2, J12.1, U5.16 (PTE9)
/PTE10: J12.13, U5.4 (PTE10)
/PTE11: J12.14, U5.3 (PTE11)
/USB_DM: J7.A7 (D-), J7.B7 (D-), U1.14 (USBD-)
/USB_DP: J7.A6 (D+), J7.B6 (D+), U1.15 (USBD+)
/V_cpu: C6.1, C7.1, C8.1, C9.1, C10.1, C11.1, C12.1, C13.1, C14.1, C17.1, J6.2, J12.9, J12.10, J13.9, J14.1 (VTref), R7.1, R9.1, R10.1, U3.8 (VCCB), U4.5 (DIR), U4.8 (VCCB), U5.7 (VDD), U5.8 (VDDA), U5.9 (VREFH), U5.41 (VDD)
/XTAL: C16.2, R6.2, U5.12 (PTB6), Y1.3
GND: C1.2, C2.2, C3.2, C4.2, C5.2, C6.2, C7.2, C8.2, C9.2, C10.2, C11.2, C12.2, C13.2, C14.2, C15.1, C16.1, C17.2, D1.1 (K), D2.1 (K), J2.1, J3.1, J4.1, J5.1, J7.A1 (GND), J7.A12 (GND), J7.B1 (GND), J7.B12 (GND), J7.S1 (SHIELD), J12.5, J12.6, J12.7, J12.8, J13.8, J14.3 (GND), J14.5 (GND), J14.9 (GNDDetect), R2.2, R4.2, R8.2, U1.11 (VBUS_SENSE), U1.13 (GND), U1.17 (PAD), U2.2 (GND), U3.4 (GND), U3.5 (DIR), U4.4 (GND), U5.10 (VSS), U5.40 (VSS), Y1.2 (G), Y1.4 (G)
unnamed: C15.2, R5.1, Y1.1
unnamed: D1.2 (A), R1.2
unnamed: D2.2 (A), R3.2
unnamed: J8.1, U3.7 (B1)
unnamed: J9.1, U3.6 (B2)
unnamed: J10.1, U4.7 (B1)
unnamed: J11.1, U4.6 (B2)
unnamed: U1.4 (GPIO4), U3.3 (A2)
unnamed: U1.3 (GPIO5), U4.3 (A2)
unnamed: U1.10 (RX), U3.2 (A1)
unnamed: U1.9 (TX), U4.2 (A1)

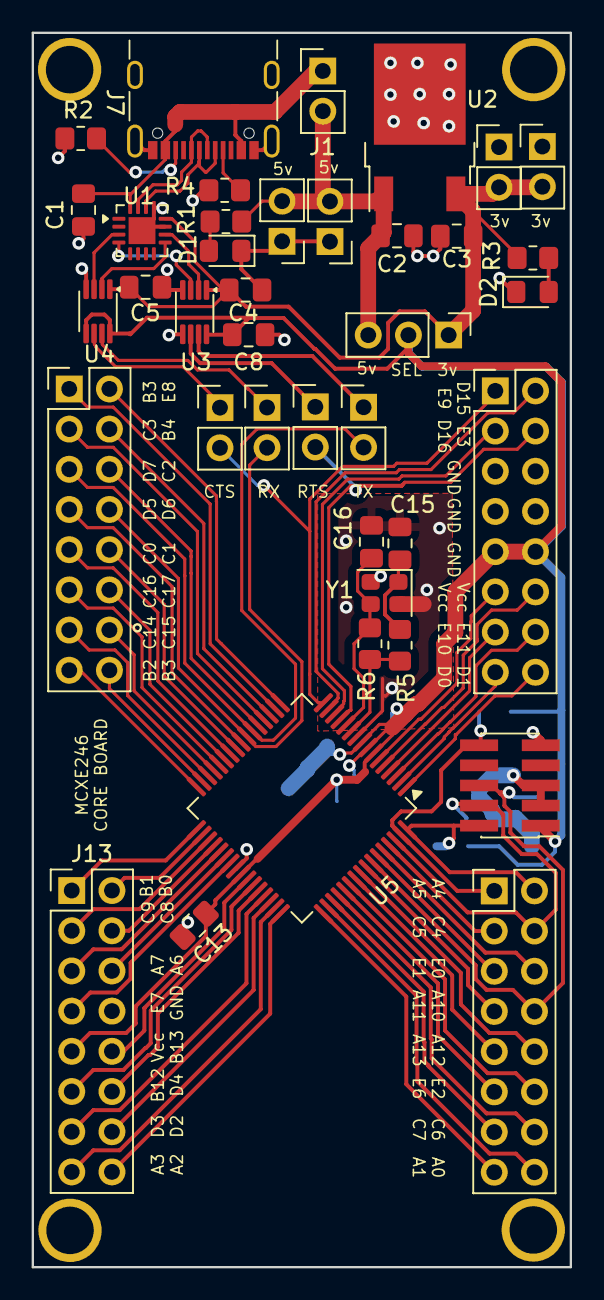
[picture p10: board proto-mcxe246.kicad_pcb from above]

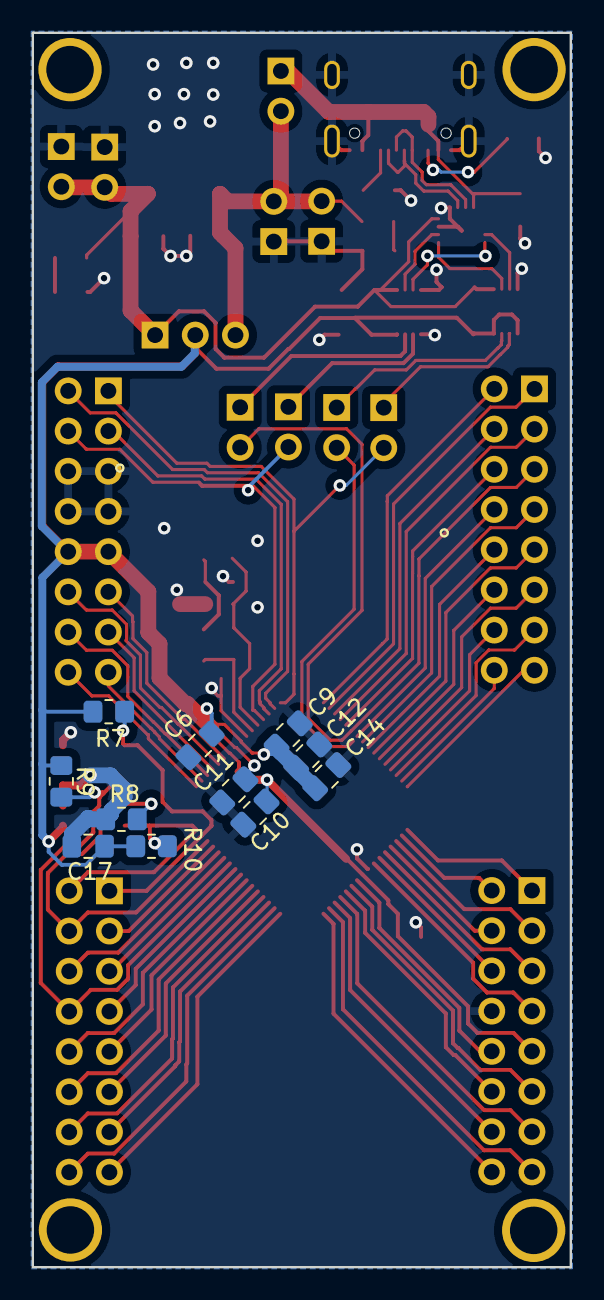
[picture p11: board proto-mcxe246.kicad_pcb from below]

Board: 2 copper layers, 34.0 x 78.0 mm, 50 parts (11 on the bottom side), 78 nets.

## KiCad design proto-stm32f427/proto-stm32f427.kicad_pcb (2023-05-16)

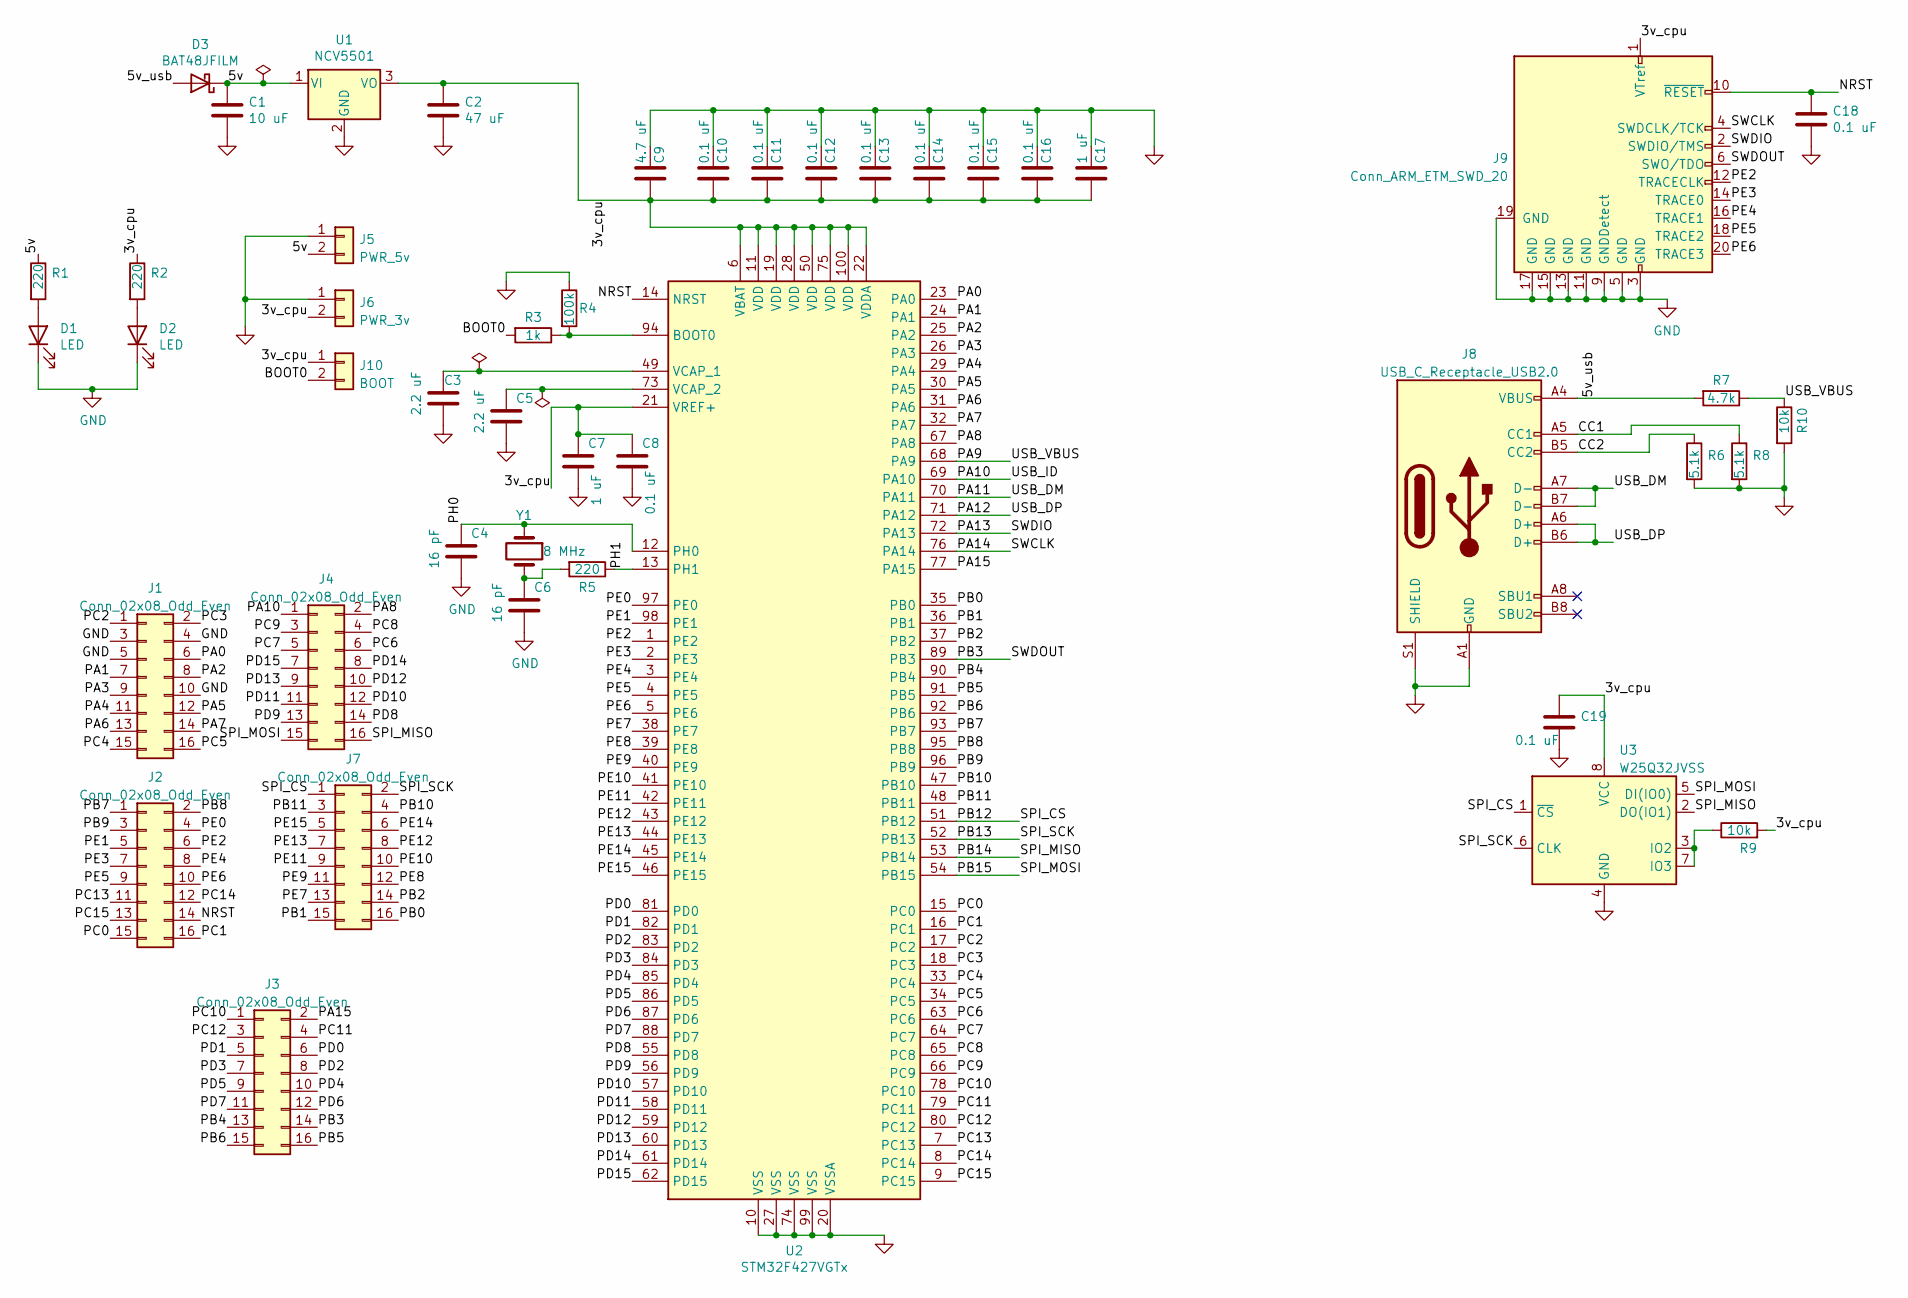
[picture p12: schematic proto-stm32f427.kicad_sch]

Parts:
C1: 10 uF; C_0805_2012Metric_Pad1.15x1.40mm_HandSolder; Digikey-Part 587-3417-1-ND
C2: 47 uF; C_0805_2012Metric_Pad1.15x1.40mm_HandSolder; Digikey-Part 718-1608-1-ND
C3, C5: 2.2 uF; C_0805_2012Metric_Pad1.15x1.40mm_HandSolder; Digikey-Part 1276-1188-1-ND
C4, C6: 16 pF; C_0805_2012Metric_Pad1.15x1.40mm_HandSolder; Digikey-Part 311-4228-1-ND
C7, C17: 1 uF; C_0805_2012Metric_Pad1.15x1.40mm_HandSolder; Digikey-Part 1276-1066-1-ND
C8, C10, C11, C12, C13, C14, C15, C16, C18: 0.1 uF; C_0805_2012Metric_Pad1.15x1.40mm_HandSolder; Digikey-Part 478-10836-1-ND
C9: 4.7 uF; C_0805_2012Metric_Pad1.15x1.40mm_HandSolder; Digikey-Part 445-14527-1-ND
C19: 0.1 uF; C_0805_2012Metric_Pad1.18x1.45mm_HandSolder
D1, D2: LED; LED_0805_2012Metric_Pad1.15x1.40mm_HandSolder; Digikey-Part 475-1415-1-ND
D3: BAT48JFILM; D_SOD-323_HandSoldering; Digikey-Part B0530WS-FDICT-ND
J1, J2, J3, J4, J7: Conn_02x08_Odd_Even; PinHeader_2x08_P2.54mm_Vertical
J5: PWR_5v; PinHeader_1x02_P2.54mm_Vertical
J6: PWR_3v; PinHeader_1x02_P2.54mm_Vertical
J8: USB_C_Receptacle_USB2.0; USB_C_Receptacle_GCT_USB4105-xx-A_16P_TopMnt_Horizontal; Digikey-Part 2073-USB4105-GF-ACT-ND
J9: Conn_ARM_ETM_SWD_20; PinHeader_2x10_P1.27mm_Vertical_SMD; Digikey-Part SAM9456-ND
J10: BOOT; PinHeader_1x02_P2.54mm_Vertical
R1, R2, R5: 220; R_0805_2012Metric_Pad1.20x1.40mm_HandSolder; Digikey-Part A129741CT-ND
R3: 1k; R_0805_2012Metric_Pad1.20x1.40mm_HandSolder; Digikey-Part RNCP0805FTD1K00CT-ND
R4: 100k; R_0805_2012Metric_Pad1.20x1.40mm_HandSolder; Digikey-Part P100KDACT-ND
R6, R8: 5.1k; R_0805_2012Metric_Pad1.20x1.40mm_HandSolder
R7: 4.7k; R_0805_2012Metric_Pad1.20x1.40mm_HandSolder; Digikey-Part 311-4.70KCRCT-ND
R9: 10k; R_0805_2012Metric_Pad1.20x1.40mm_HandSolder
R10: 10k; R_0805_2012Metric_Pad1.20x1.40mm_HandSolder; Digikey-Part RNCF0805DTE10K0CT-ND
U1: NCV5501; TO-252-2; Digikey-Part NCV5501DT33GOS-ND
U2: STM32F427VGTx; LQFP-100_14x14mm_P0.5mm; Digikey-Part 497-16769-ND
U3: W25Q32JVSS; SOIC-8_5.23x5.23mm_P1.27mm
Y1: 8 MHz; Crystal_HC49-U_Vertical; Digikey-Part 535-10212-1-ND

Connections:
/3v_cpu: C2.1, C7.1, C8.1, C9.2, C10.2, C11.2, C12.2, C13.2, C14.2, C15.2, C16.2, C17.2, C19.1, J6.2, J9.1 (VTref), J10.1, R2.1, R9.2, U1.3 (VO), U2.6 (VBAT), U2.11 (VDD), U2.19 (VDD), U2.21 (VREF+), U2.22 (VDDA), U2.28 (VDD), U2.50 (VDD), U2.75 (VDD), U2.100 (VDD), U3.8 (VCC)
/5v: C1.1, D3.1 (K), J5.2, R1.1, U1.1 (VI)
/5v_usb: D3.2 (A), J8.A4 (VBUS), J8.A9 (VBUS), J8.B4 (VBUS), J8.B9 (VBUS), R7.2
/BOOT0: J10.2, R3.2
/CC1: J8.A5 (CC1), R8.1
/CC2: J8.B5 (CC2), R6.1
/NRST: C18.1, J2.14, J9.10 (~RESET), U2.14 (NRST)
/PA0: J1.6, U2.23 (PA0)
/PA1: J1.7, U2.24 (PA1)
/PA2: J1.8, U2.25 (PA2)
/PA3: J1.9, U2.26 (PA3)
/PA4: J1.11, U2.29 (PA4)
/PA5: J1.12, U2.30 (PA5)
/PA6: J1.13, U2.31 (PA6)
/PA7: J1.14, U2.32 (PA7)
/PA8: J4.2, U2.67 (PA8)
/PA9: R7.1, R10.1, U2.68 (PA9)
/PA10: J4.1, U2.69 (PA10)
/PA11: J8.A7 (D-), J8.B7 (D-), U2.70 (PA11)
/PA12: J8.A6 (D+), J8.B6 (D+), U2.71 (PA12)
/PA13: J9.2 (SWDIO/TMS), U2.72 (PA13)
/PA14: J9.4 (SWDCLK/TCK), U2.76 (PA14)
/PA15: J3.2, U2.77 (PA15)
/PB0: J7.16, U2.35 (PB0)
/PB1: J7.15, U2.36 (PB1)
/PB2: J7.14, U2.37 (PB2)
/PB3: J3.14, J9.6 (SWO/TDO), U2.89 (PB3)
/PB4: J3.13, U2.90 (PB4)
/PB5: J3.16, U2.91 (PB5)
/PB6: J3.15, U2.92 (PB6)
/PB7: J2.1, U2.93 (PB7)
/PB8: J2.2, U2.95 (PB8)
/PB9: J2.3, U2.96 (PB9)
/PB10: J7.4, U2.47 (PB10)
/PB11: J7.3, U2.48 (PB11)
/PB12: J7.1, U2.51 (PB12), U3.1 (~CS)
/PB13: J7.2, U2.52 (PB13), U3.6 (CLK)
/PB14: J4.16, U2.53 (PB14), U3.2 (DO(IO1))
/PB15: J4.15, U2.54 (PB15), U3.5 (DI(IO0))
/PC0: J2.15, U2.15 (PC0)
/PC1: J2.16, U2.16 (PC1)
/PC2: J1.1, U2.17 (PC2)
/PC3: J1.2, U2.18 (PC3)
/PC4: J1.15, U2.33 (PC4)
/PC5: J1.16, U2.34 (PC5)
/PC6: J4.6, U2.63 (PC6)
/PC7: J4.5, U2.64 (PC7)
/PC8: J4.4, U2.65 (PC8)
/PC9: J4.3, U2.66 (PC9)
/PC10: J3.1, U2.78 (PC10)
/PC11: J3.4, U2.79 (PC11)
/PC12: J3.3, U2.80 (PC12)
/PC13: J2.11, U2.7 (PC13)
/PC14: J2.12, U2.8 (PC14)
/PC15: J2.13, U2.9 (PC15)
/PD0: J3.6, U2.81 (PD0)
/PD1: J3.5, U2.82 (PD1)
/PD2: J3.8, U2.83 (PD2)
/PD3: J3.7, U2.84 (PD3)
/PD4: J3.10, U2.85 (PD4)
/PD5: J3.9, U2.86 (PD5)
/PD6: J3.12, U2.87 (PD6)
/PD7: J3.11, U2.88 (PD7)
/PD8: J4.14, U2.55 (PD8)
/PD9: J4.13, U2.56 (PD9)
/PD10: J4.12, U2.57 (PD10)
/PD11: J4.11, U2.58 (PD11)
/PD12: J4.10, U2.59 (PD12)
/PD13: J4.9, U2.60 (PD13)
/PD14: J4.8, U2.61 (PD14)
/PD15: J4.7, U2.62 (PD15)
/PE0: J2.4, U2.97 (PE0)
/PE1: J2.5, U2.98 (PE1)
/PE2: J2.6, J9.12 (TRACECLK), U2.1 (PE2)
/PE3: J2.7, J9.14 (TRACE0), U2.2 (PE3)
/PE4: J2.8, J9.16 (TRACE1), U2.3 (PE4)
/PE5: J2.9, J9.18 (TRACE2), U2.4 (PE5)
/PE6: J2.10, J9.20 (TRACE3), U2.5 (PE6)
/PE7: J7.13, U2.38 (PE7)
/PE8: J7.12, U2.39 (PE8)
/PE9: J7.11, U2.40 (PE9)
/PE10: J7.10, U2.41 (PE10)
/PE11: J7.9, U2.42 (PE11)
/PE12: J7.8, U2.43 (PE12)
/PE13: J7.7, U2.44 (PE13)
/PE14: J7.6, U2.45 (PE14)
/PE15: J7.5, U2.46 (PE15)
/PH0: C4.2, U2.12 (PH0), Y1.1
/PH1: R5.1, U2.13 (PH1)
GND: C1.2, C2.2, C3.2, C4.1, C5.2, C6.1, C7.2, C8.2, C9.1, C10.1, C11.1, C12.1, C13.1, C14.1, C15.1, C16.1, C17.1, C18.2, C19.2, D1.1 (K), D2.1 (K), J1.3, J1.4, J1.5, J1.10, J5.1, J6.1, J8.A1 (GND), J8.A12 (GND), J8.B1 (GND), J8.B12 (GND), J8.S1 (SHIELD), J9.3 (GND), J9.5 (GND), J9.9 (GNDDetect), J9.11 (GND), J9.13 (GND), J9.15 (GND), J9.17 (GND), J9.19 (GND), R4.1, R6.2, R8.2, R10.2, U1.2 (GND), U2.10 (VSS), U2.20 (VSSA), U2.27 (VSS), U2.74 (VSS), U2.99 (VSS), U3.4 (GND)
unnamed: C3.1, U2.49 (VCAP_1)
unnamed: C5.1, U2.73 (VCAP_2)
unnamed: C6.2, R5.2, Y1.2
unnamed: D1.2 (A), R1.2
unnamed: D2.2 (A), R2.2
unnamed: R3.1, R4.2, U2.94 (BOOT0)
unnamed: R9.1, U3.3 (IO2), U3.7 (IO3)

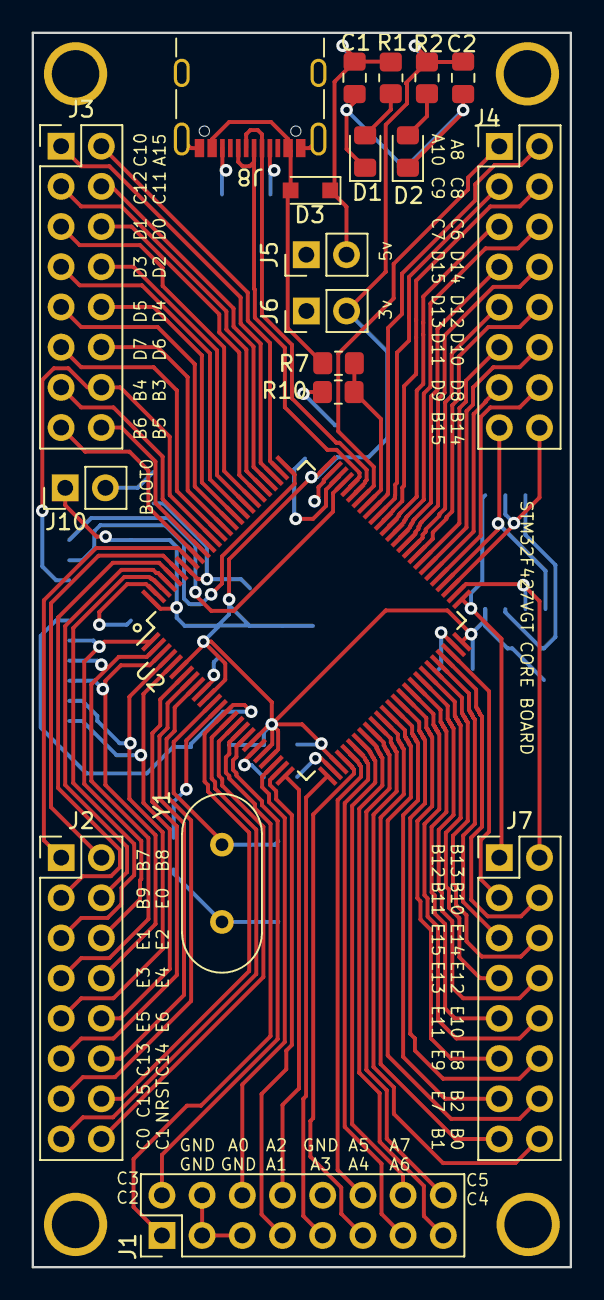
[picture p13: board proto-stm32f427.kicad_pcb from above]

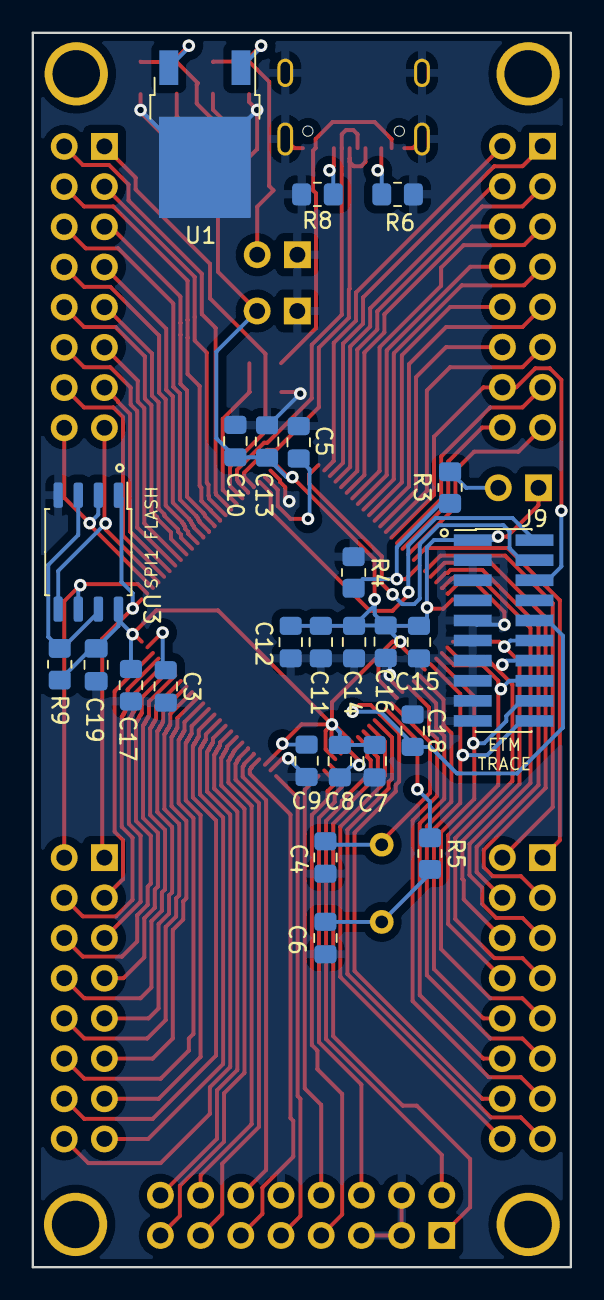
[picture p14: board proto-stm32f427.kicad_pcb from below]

Board: 2 copper layers, 34.0 x 78.0 mm, 46 parts (26 on the bottom side), 97 nets.

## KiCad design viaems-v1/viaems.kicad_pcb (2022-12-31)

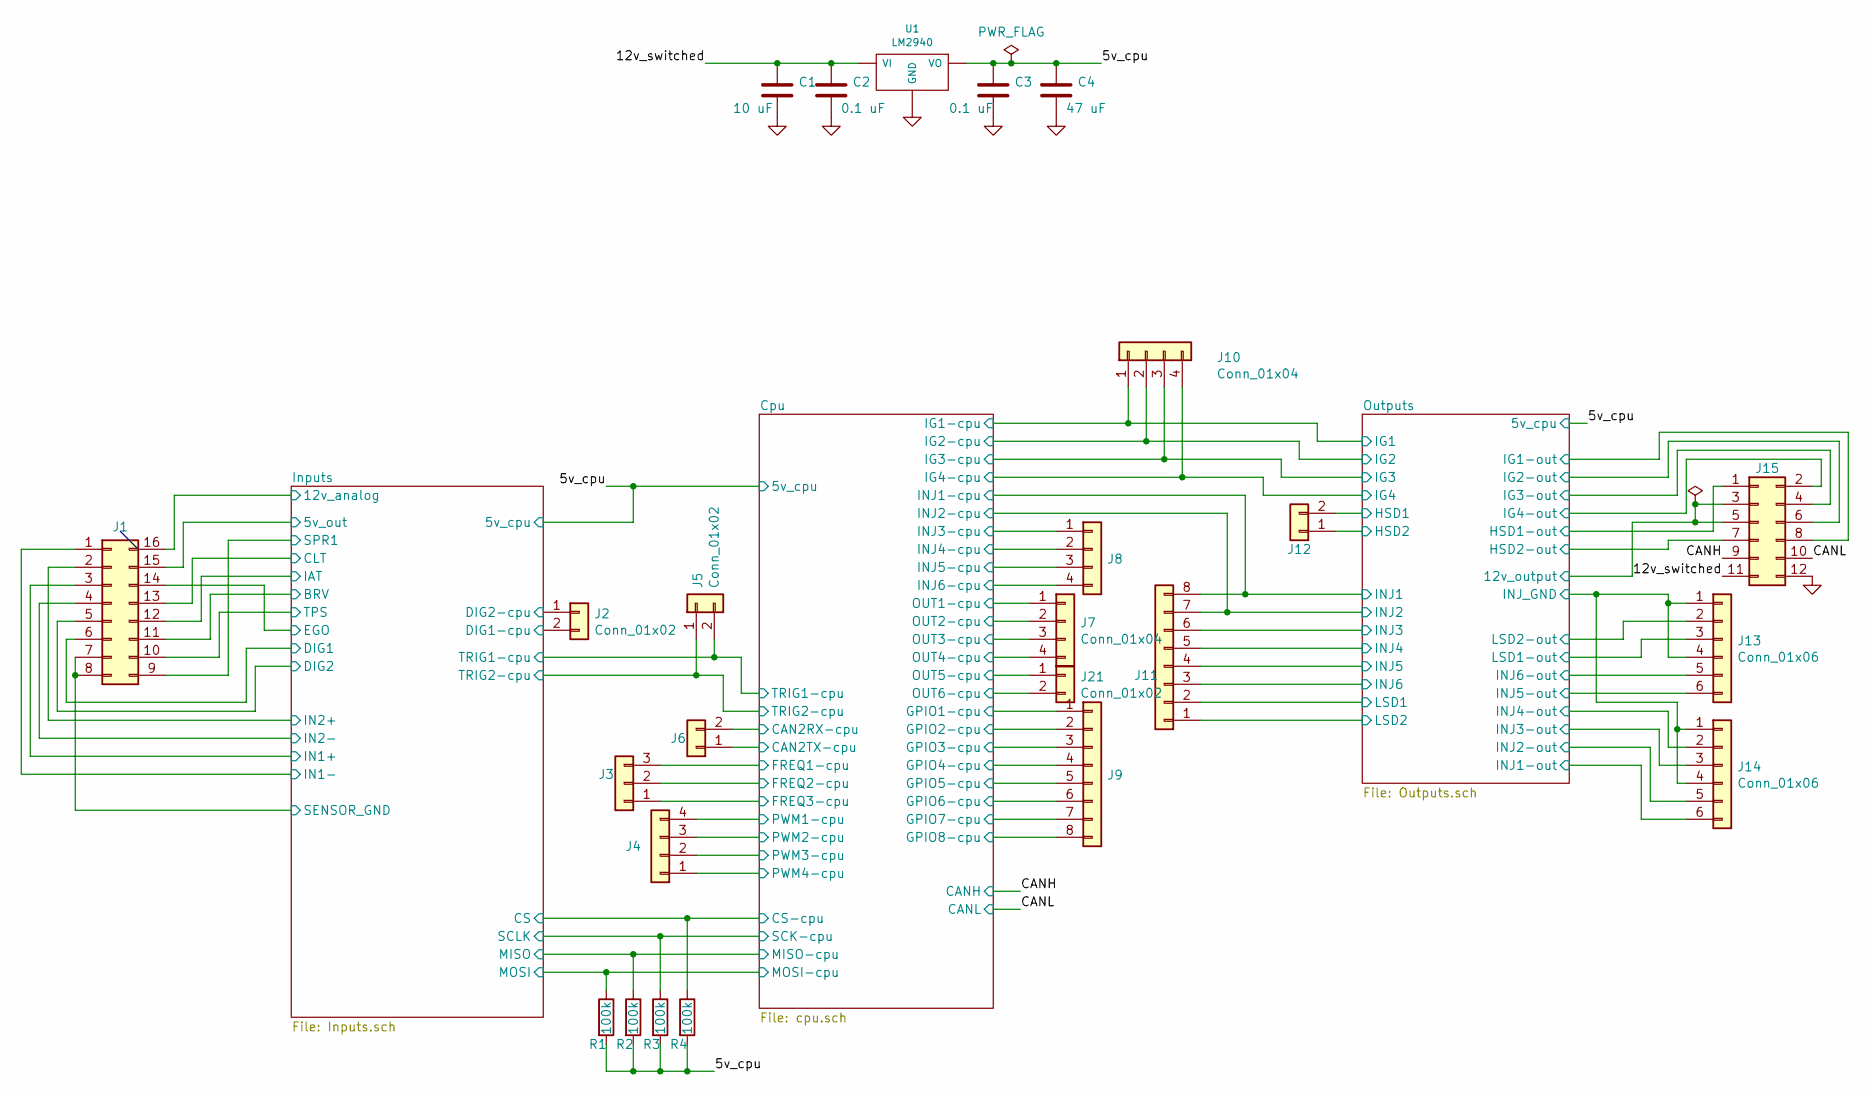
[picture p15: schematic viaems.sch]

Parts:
C1: 10 uF; C_1206_3216Metric_Pad1.42x1.75mm_HandSolder; Digikey-Part 445-8034-1-ND
C2, C3: 0.1 uF; C_0805_2012Metric_Pad1.15x1.40mm_HandSolder; Digikey-Part 478-10836-1-ND
C4: 47 uF; C_1206_3216Metric_Pad1.42x1.75mm_HandSolder; Digikey-Part 478-9009-1-ND
J1: Conn_02x08_Counter_Clockwise; PinHeader_2x08_P2.54mm_Vertical; Digikey-Part 609-3220-ND
J2, J5, J6, J12, J21: Conn_01x02; PinHeader_1x02_P2.54mm_Vertical; Digikey-Part 952-2262-ND
J3: Conn_01x03; PinHeader_1x03_P2.54mm_Vertical; Digikey-Part 732-5316-ND
J4, J7, J8, J10: Conn_01x04; PinHeader_1x04_P2.54mm_Vertical; Digikey-Part 732-5317-ND
J9, J11: Conn_01x08; PinHeader_1x08_P2.54mm_Vertical; Digikey-Part 732-5321-ND
J13, J14: Conn_01x06; PinHeader_1x06_P2.54mm_Vertical; Digikey-Part 732-5319-ND
J15: Conn_02x06_Odd_Even; PinHeader_2x06_P2.54mm_Vertical; Digikey-Part 732-5297-ND
R1, R2, R3, R4: 100k; R_0805_2012Metric_Pad1.15x1.40mm_HandSolder; Digikey-Part P100KDACT-ND
U1: LM2940; TO-220-3_Horizontal_TabDown; Digikey-Part LM2940T-5.0/NOPB-ND

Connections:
5v_cpu: C3.1, C4.1, R1.2, R2.2, R3.2, R4.2, U1.3 (VO); also elsewhere on the board
/12v_switched: C1.1, C2.1, J15.11, U1.1 (VI)
/CANH: J15.9; also elsewhere on the board
/CANL: J15.10; also elsewhere on the board
/Cpu/CAN2RX-cpu: J6.2; also elsewhere on the board
/Cpu/CAN2TX-cpu: J6.1; also elsewhere on the board
/Cpu/FREQ1-cpu: J3.3; also elsewhere on the board
/Cpu/FREQ2-cpu: J3.2; also elsewhere on the board
/Cpu/FREQ3-cpu: J3.1; also elsewhere on the board
/Cpu/GPIO1-cpu: J9.1; also elsewhere on the board
/Cpu/GPIO2-cpu: J9.2; also elsewhere on the board
/Cpu/GPIO3-cpu: J9.3; also elsewhere on the board
/Cpu/GPIO4-cpu: J9.4; also elsewhere on the board
/Cpu/GPIO5-cpu: J9.5; also elsewhere on the board
/Cpu/GPIO6-cpu: J9.6; also elsewhere on the board
/Cpu/GPIO7-cpu: J9.7; also elsewhere on the board
/Cpu/GPIO8-cpu: J9.8; also elsewhere on the board
/Cpu/INJ3-cpu: J8.1; also elsewhere on the board
/Cpu/INJ4-cpu: J8.2; also elsewhere on the board
/Cpu/INJ5-cpu: J8.3; also elsewhere on the board
/Cpu/INJ6-cpu: J8.4; also elsewhere on the board
/Cpu/OUT1-cpu: J7.1; also elsewhere on the board
/Cpu/OUT2-cpu: J7.2; also elsewhere on the board
/Cpu/OUT3-cpu: J7.3; also elsewhere on the board
/Cpu/OUT4-cpu: J7.4; also elsewhere on the board
/Cpu/OUT5-cpu: J21.1; also elsewhere on the board
/Cpu/OUT6-cpu: J21.2; also elsewhere on the board
/Cpu/PWM1-cpu: J4.4; also elsewhere on the board
/Cpu/PWM2-cpu: J4.3; also elsewhere on the board
/Cpu/PWM3-cpu: J4.2; also elsewhere on the board
/Cpu/PWM4-cpu: J4.1; also elsewhere on the board
/Cpu/SCK-cpu: R3.1; also elsewhere on the board
/Cpu/TRIG1-cpu: J5.2; also elsewhere on the board
/Cpu/TRIG2-cpu: J5.1; also elsewhere on the board
/Inputs/5v_out: J1.15; also elsewhere on the board
/Inputs/12v_analog: J1.16; also elsewhere on the board
/Inputs/BRV: J1.11; also elsewhere on the board
/Inputs/CLT: J1.13; also elsewhere on the board
/Inputs/CS: R4.1; also elsewhere on the board
/Inputs/DIG1: J1.6; also elsewhere on the board
/Inputs/DIG1-cpu: J2.2; also elsewhere on the board
/Inputs/DIG2: J1.5; also elsewhere on the board
/Inputs/DIG2-cpu: J2.1; also elsewhere on the board
/Inputs/EGO: J1.14; also elsewhere on the board
/Inputs/IAT: J1.12; also elsewhere on the board
/Inputs/IN1+: J1.3; also elsewhere on the board
/Inputs/IN1-: J1.1; also elsewhere on the board
/Inputs/IN2+: J1.2; also elsewhere on the board
/Inputs/IN2-: J1.4; also elsewhere on the board
/Inputs/MISO: R2.1; also elsewhere on the board
/Inputs/MOSI: R1.1; also elsewhere on the board
/Inputs/SPR1: J1.9; also elsewhere on the board
/Inputs/TPS: J1.10; also elsewhere on the board
/Outputs/12v_output: J15.3, J15.5; also elsewhere on the board
/Outputs/HSD1: J12.2; also elsewhere on the board
/Outputs/HSD1-out: J15.1; also elsewhere on the board
/Outputs/HSD2: J12.1; also elsewhere on the board
/Outputs/HSD2-out: J15.7; also elsewhere on the board
/Outputs/IG1: J10.1; also elsewhere on the board
/Outputs/IG1-out: J15.8; also elsewhere on the board
/Outputs/IG2: J10.2; also elsewhere on the board
/Outputs/IG2-out: J15.6; also elsewhere on the board
/Outputs/IG3: J10.3; also elsewhere on the board
/Outputs/IG3-out: J15.4; also elsewhere on the board
/Outputs/IG4: J10.4; also elsewhere on the board
/Outputs/IG4-out: J15.2; also elsewhere on the board
/Outputs/INJ1: J11.8; also elsewhere on the board
/Outputs/INJ1-out: J14.6; also elsewhere on the board
/Outputs/INJ2: J11.7; also elsewhere on the board
/Outputs/INJ2-out: J14.5; also elsewhere on the board
/Outputs/INJ3: J11.6; also elsewhere on the board
/Outputs/INJ3-out: J14.3; also elsewhere on the board
/Outputs/INJ4: J11.5; also elsewhere on the board
/Outputs/INJ4-out: J14.2; also elsewhere on the board
/Outputs/INJ5: J11.4; also elsewhere on the board
/Outputs/INJ5-out: J13.6; also elsewhere on the board
/Outputs/INJ6: J11.3; also elsewhere on the board
/Outputs/INJ6-out: J13.5; also elsewhere on the board
/Outputs/INJ_GND: J13.1, J13.4, J14.1, J14.4; also elsewhere on the board
/Outputs/LSD1: J11.2; also elsewhere on the board
/Outputs/LSD1-out: J13.3; also elsewhere on the board
/Outputs/LSD2: J11.1; also elsewhere on the board
/Outputs/LSD2-out: J13.2; also elsewhere on the board
GND: C1.2, C2.2, C3.2, C4.2, J1.7, J1.8, J15.12, U1.2 (GND); also elsewhere on the board

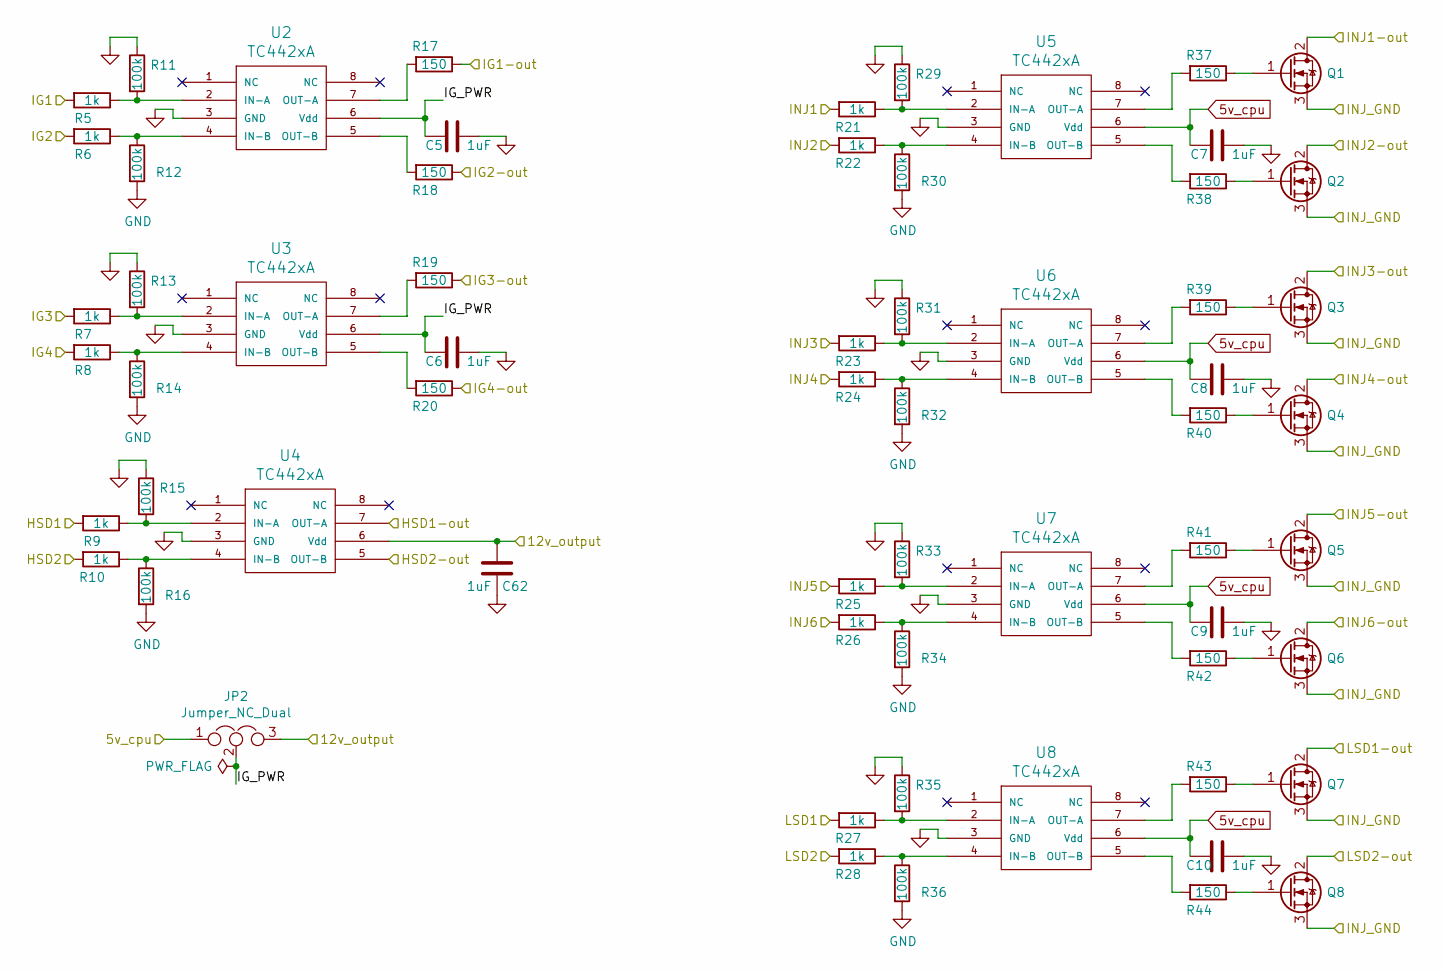
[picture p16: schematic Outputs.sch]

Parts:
C5, C6, C7, C8, C9, C10, C62: 1uF; C_0805_2012Metric_Pad1.15x1.40mm_HandSolder; Digikey-Part 1276-1029-1-ND
JP2: Jumper_NC_Dual; PinHeader_1x03_P2.54mm_Vertical; Digikey-Part 732-5316-ND
Q1, Q2, Q3, Q4, Q5, Q6, Q7, Q8: VND7NV04; TO-252-2; Digikey-Part 497-11707-1-ND
R5, R6, R7, R8, R9, R10, R21, R22, R23, R24, R25, R26, R27, R28: 1k; R_0805_2012Metric_Pad1.15x1.40mm_HandSolder; Digikey-Part RNCP0805FTD1K00CT-ND
R11, R12, R13, R14, R15, R16, R29, R30, R31, R32, R33, R34, R35, R36: 100k; R_0805_2012Metric_Pad1.15x1.40mm_HandSolder; Digikey-Part P100KDACT-ND
R17, R18, R19, R20: 150; R_2512_6332Metric_Pad1.52x3.35mm_HandSolder; Digikey-Part 541-150XCT-ND
R37, R38, R39, R40, R41, R42, R43, R44: 150; R_0805_2012Metric_Pad1.15x1.40mm_HandSolder; Digikey-Part RNCP0805FTD150RCT-ND
U2, U3, U4, U5, U6, U7, U8: TC442xA; SOIC-8_3.9x4.9mm_P1.27mm; Digikey-Part TC4427EOA713CT-ND

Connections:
5v_cpu: C7.2, C8.2, C9.2, C10.2, JP2.1, U5.6 (Vdd), U6.6 (Vdd), U7.6 (Vdd), U8.6 (Vdd); also elsewhere on the board
/Outputs/12v_output: C62.2, JP2.3, U4.6 (Vdd); also elsewhere on the board
/Outputs/HSD1: R9.2; also elsewhere on the board
/Outputs/HSD1-out: U4.7 (OUT-A); also elsewhere on the board
/Outputs/HSD2: R10.2; also elsewhere on the board
/Outputs/HSD2-out: U4.5 (OUT-B); also elsewhere on the board
/Outputs/IG1: R5.2; also elsewhere on the board
/Outputs/IG1-out: R17.1; also elsewhere on the board
/Outputs/IG2: R6.2; also elsewhere on the board
/Outputs/IG2-out: R18.1; also elsewhere on the board
/Outputs/IG3: R7.2; also elsewhere on the board
/Outputs/IG3-out: R19.1; also elsewhere on the board
/Outputs/IG4: R8.2; also elsewhere on the board
/Outputs/IG4-out: R20.1; also elsewhere on the board
/Outputs/IG_PWR: C5.2, C6.2, JP2.2, U2.6 (Vdd), U3.6 (Vdd)
/Outputs/INJ1: R21.2; also elsewhere on the board
/Outputs/INJ1-out: Q1.2 (D); also elsewhere on the board
/Outputs/INJ2: R22.2; also elsewhere on the board
/Outputs/INJ2-out: Q2.2 (D); also elsewhere on the board
/Outputs/INJ3: R23.2; also elsewhere on the board
/Outputs/INJ3-out: Q3.2 (D); also elsewhere on the board
/Outputs/INJ4: R24.2; also elsewhere on the board
/Outputs/INJ4-out: Q4.2 (D); also elsewhere on the board
/Outputs/INJ5: R25.2; also elsewhere on the board
/Outputs/INJ5-out: Q5.2 (D); also elsewhere on the board
/Outputs/INJ6: R26.2; also elsewhere on the board
/Outputs/INJ6-out: Q6.2 (D); also elsewhere on the board
/Outputs/INJ_GND: Q1.3 (S), Q2.3 (S), Q3.3 (S), Q4.3 (S), Q5.3 (S), Q6.3 (S), Q7.3 (S), Q8.3 (S); also elsewhere on the board
/Outputs/LSD1: R27.2; also elsewhere on the board
/Outputs/LSD1-out: Q7.2 (D); also elsewhere on the board
/Outputs/LSD2: R28.2; also elsewhere on the board
/Outputs/LSD2-out: Q8.2 (D); also elsewhere on the board
GND: C5.1, C6.1, C7.1, C8.1, C9.1, C10.1, C62.1, R11.1, R12.2, R13.1, R14.2, R15.1, R16.2, R29.1, R30.2, R31.1, R32.2, R33.1, R34.2, R35.1, R36.2, U2.3 (GND), U3.3 (GND), U4.3 (GND), U5.3 (GND), U6.3 (GND), U7.3 (GND), U8.3 (GND); also elsewhere on the board
unnamed: Q1.1 (G), R37.1
unnamed: Q2.1 (G), R38.1
unnamed: Q3.1 (G), R39.1
unnamed: Q4.1 (G), R40.1
unnamed: Q5.1 (G), R41.1
unnamed: Q6.1 (G), R42.1
unnamed: Q7.1 (G), R43.1
unnamed: Q8.1 (G), R44.1
unnamed: R10.1, R16.1, U4.4 (IN-B)
unnamed: R5.1, R11.2, U2.2 (IN-A)
unnamed: R6.1, R12.1, U2.4 (IN-B)
unnamed: R7.1, R13.2, U3.2 (IN-A)
unnamed: R8.1, R14.1, U3.4 (IN-B)
unnamed: R9.1, R15.2, U4.2 (IN-A)
unnamed: R17.2, U2.7 (OUT-A)
unnamed: R18.2, U2.5 (OUT-B)
unnamed: R19.2, U3.7 (OUT-A)
unnamed: R20.2, U3.5 (OUT-B)
unnamed: R21.1, R29.2, U5.2 (IN-A)
unnamed: R22.1, R30.1, U5.4 (IN-B)
unnamed: R23.1, R31.2, U6.2 (IN-A)
unnamed: R24.1, R32.1, U6.4 (IN-B)
unnamed: R25.1, R33.2, U7.2 (IN-A)
unnamed: R26.1, R34.1, U7.4 (IN-B)
unnamed: R27.1, R35.2, U8.2 (IN-A)
unnamed: R28.1, R36.1, U8.4 (IN-B)
unnamed: R37.2, U5.7 (OUT-A)
unnamed: R38.2, U5.5 (OUT-B)
unnamed: R39.2, U6.7 (OUT-A)
unnamed: R40.2, U6.5 (OUT-B)
unnamed: R41.2, U7.7 (OUT-A)
unnamed: R42.2, U7.5 (OUT-B)
unnamed: R43.2, U8.7 (OUT-A)
unnamed: R44.2, U8.5 (OUT-B)

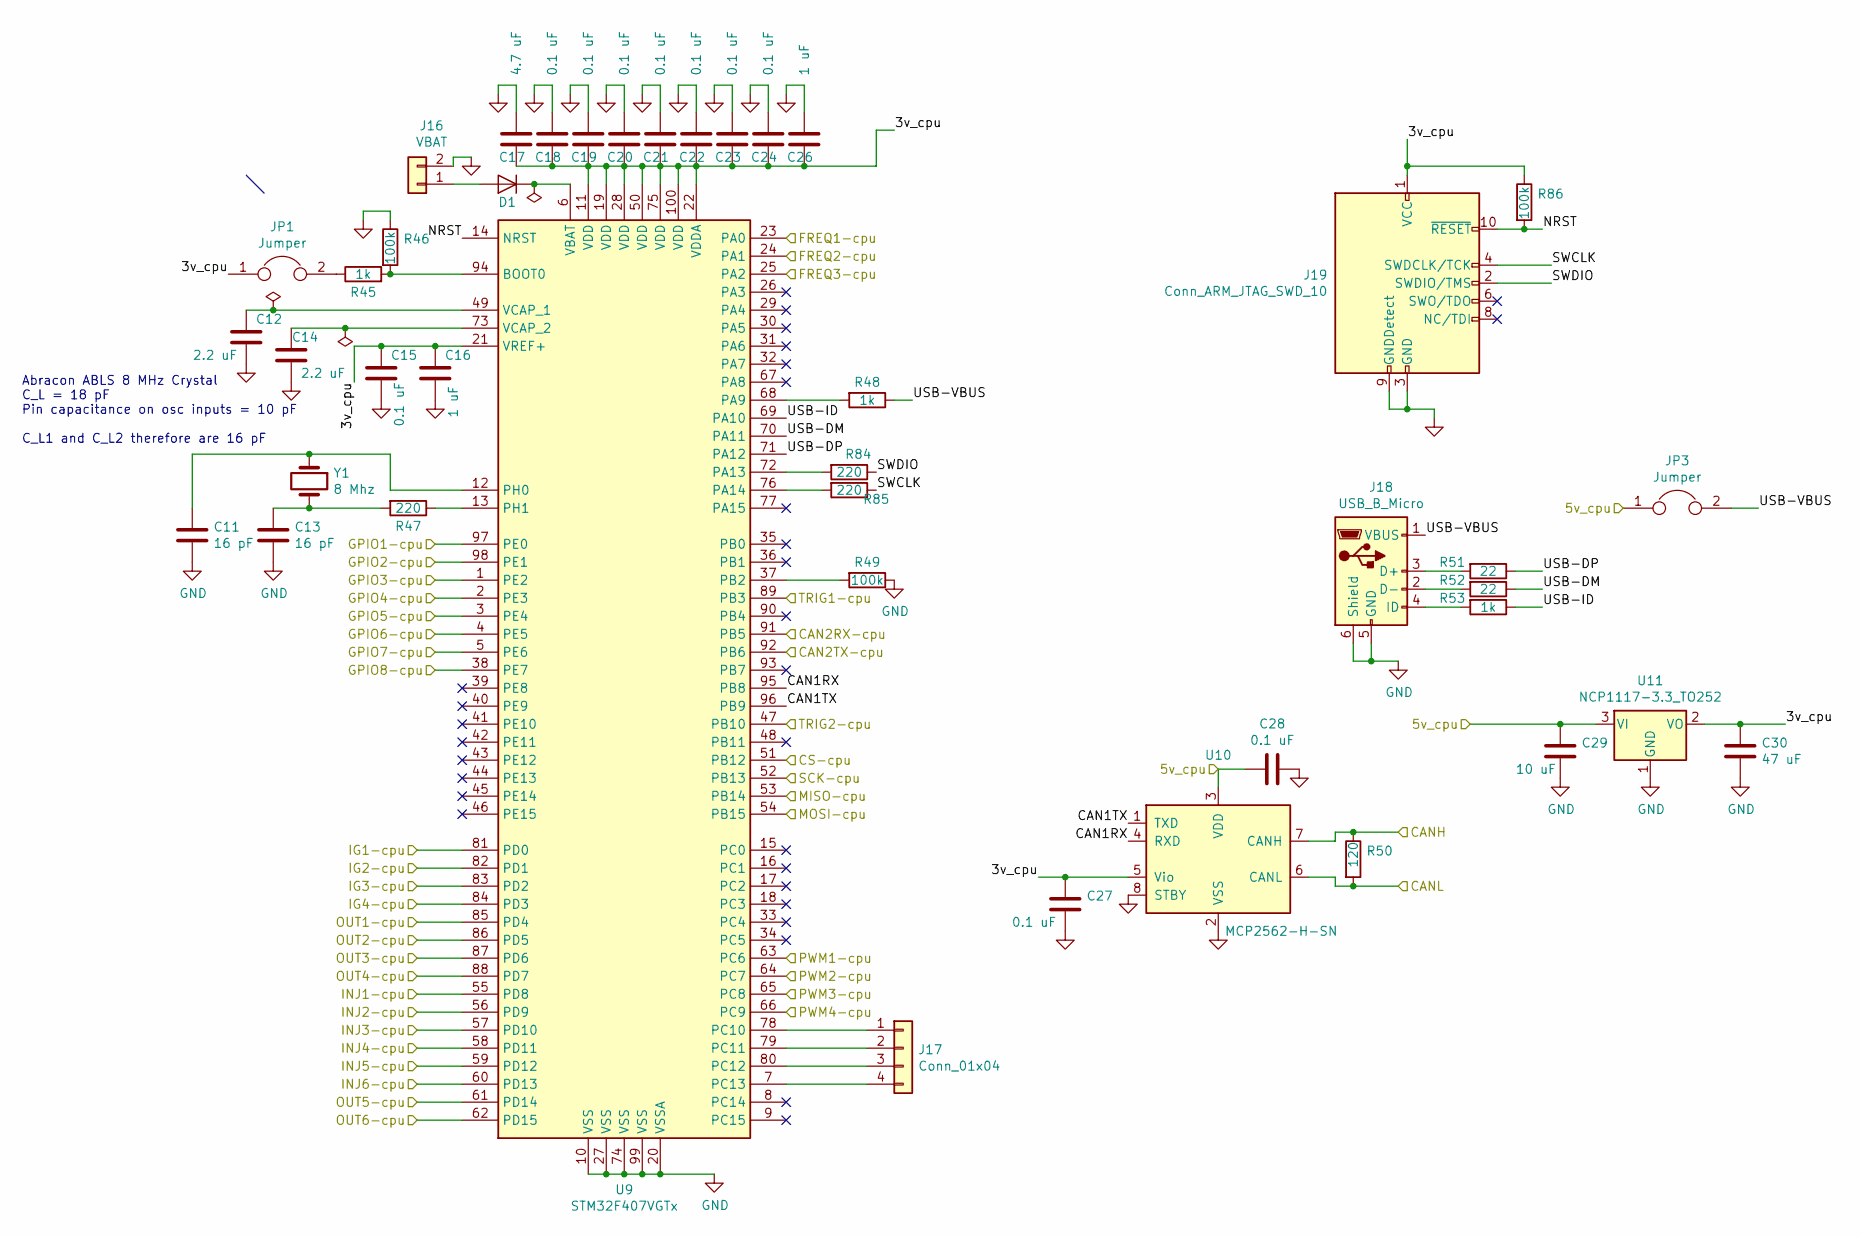
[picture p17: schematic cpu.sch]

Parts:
C11, C13: 16 pF; C_0805_2012Metric_Pad1.15x1.40mm_HandSolder; Digikey-Part 311-4228-1-ND
C12, C14: 2.2 uF; C_0805_2012Metric_Pad1.15x1.40mm_HandSolder; Digikey-Part 1276-1188-1-ND
C15, C18, C19, C20, C21, C22, C23, C24, C27, C28: 0.1 uF; C_0805_2012Metric_Pad1.15x1.40mm_HandSolder; Digikey-Part 478-10836-1-ND
C16, C26: 1 uF; C_0805_2012Metric_Pad1.15x1.40mm_HandSolder; Digikey-Part 1276-1066-1-ND
C17: 4.7 uF; C_0805_2012Metric_Pad1.15x1.40mm_HandSolder; Digikey-Part 445-14527-1-ND
C29: 10 uF; C_0805_2012Metric_Pad1.15x1.40mm_HandSolder; Digikey-Part 587-3417-1-ND
C30: 47 uF; C_1206_3216Metric_Pad1.42x1.75mm_HandSolder; Digikey-Part 478-9009-1-ND
D1: D; D_0805_2012Metric_Pad1.15x1.40mm_HandSolder; Digikey-Part 478-7802-1-ND
J16: VBAT; PinHeader_1x02_P2.54mm_Vertical; Digikey-Part 952-2262-ND
J17: Conn_01x04; PinHeader_1x04_P2.54mm_Vertical; Digikey-Part 732-5317-ND
J18: USB_B_Micro; USB_Micro-B_Amphenol_10103594-0001LF_Horizontal; Digikey-Part 609-4050-1-ND
J19: Conn_ARM_JTAG_SWD_10; PinHeader_2x05_P1.27mm_Vertical_SMD; Digikey-Part SAM9438-ND
JP1, JP3: Jumper; PinHeader_1x02_P2.54mm_Vertical; Digikey-Part 952-2262-ND
R45, R48, R53: 1k; R_0805_2012Metric_Pad1.15x1.40mm_HandSolder; Digikey-Part RNCP0805FTD1K00CT-ND
R46, R49, R86: 100k; R_0805_2012Metric_Pad1.15x1.40mm_HandSolder; Digikey-Part P100KDACT-ND
R47, R84, R85: 220; R_0805_2012Metric_Pad1.15x1.40mm_HandSolder; Digikey-Part A129741CT-ND
R50: 120; R_0805_2012Metric_Pad1.15x1.40mm_HandSolder; Digikey-Part P16874CT-ND
R51, R52: 22; R_0805_2012Metric_Pad1.15x1.40mm_HandSolder; Digikey-Part A130124CT-ND
U9: STM32F407VGTx; LQFP-100_14x14mm_P0.5mm; Digikey-Part 497-17438-ND
U10: MCP2562-H-SN; SOIC-8_3.9x4.9mm_P1.27mm; Digikey-Part MCP2562-H/SN
U11: NCP1117-3.3_TO252; TO-252-2; Digikey-Part NCP1117DT33T5GOSCT-ND
Y1: 8 Mhz; Crystal_HC49-U_Vertical; Digikey-Part 535-10212-1-ND

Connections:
5v_cpu: C28.2, C29.1, JP3.1, U10.3 (VDD), U11.3 (VI); also elsewhere on the board
/CANH: R50.1, U10.7 (CANH); also elsewhere on the board
/CANL: R50.2, U10.6 (CANL); also elsewhere on the board
/Cpu/3v_cpu: C15.1, C16.1, C17.2, C18.2, C19.2, C20.2, C21.2, C22.2, C23.2, C24.2, C26.2, C27.1, C30.1, J19.1 (VCC), JP1.1, R86.1, U9.11 (VDD), U9.19 (VDD), U9.21 (VREF+), U9.22 (VDDA), U9.28 (VDD), U9.50 (VDD), U9.75 (VDD), U9.100 (VDD), U10.5 (Vio), U11.2 (VO)
/Cpu/CAN1RX: U9.95 (PB8), U10.4 (RXD)
/Cpu/CAN1TX: U9.96 (PB9), U10.1 (TXD)
/Cpu/CAN2RX-cpu: U9.91 (PB5); also elsewhere on the board
/Cpu/CAN2TX-cpu: U9.92 (PB6); also elsewhere on the board
/Cpu/FREQ1-cpu: U9.23 (PA0); also elsewhere on the board
/Cpu/FREQ2-cpu: U9.24 (PA1); also elsewhere on the board
/Cpu/FREQ3-cpu: U9.25 (PA2); also elsewhere on the board
/Cpu/GPIO1-cpu: U9.97 (PE0); also elsewhere on the board
/Cpu/GPIO2-cpu: U9.98 (PE1); also elsewhere on the board
/Cpu/GPIO3-cpu: U9.1 (PE2); also elsewhere on the board
/Cpu/GPIO4-cpu: U9.2 (PE3); also elsewhere on the board
/Cpu/GPIO5-cpu: U9.3 (PE4); also elsewhere on the board
/Cpu/GPIO6-cpu: U9.4 (PE5); also elsewhere on the board
/Cpu/GPIO7-cpu: U9.5 (PE6); also elsewhere on the board
/Cpu/GPIO8-cpu: U9.38 (PE7); also elsewhere on the board
/Cpu/INJ3-cpu: U9.57 (PD10); also elsewhere on the board
/Cpu/INJ4-cpu: U9.58 (PD11); also elsewhere on the board
/Cpu/INJ5-cpu: U9.59 (PD12); also elsewhere on the board
/Cpu/INJ6-cpu: U9.60 (PD13); also elsewhere on the board
/Cpu/NRST: J19.10 (~RESET~), R86.2, U9.14 (NRST)
/Cpu/OUT1-cpu: U9.85 (PD4); also elsewhere on the board
/Cpu/OUT2-cpu: U9.86 (PD5); also elsewhere on the board
/Cpu/OUT3-cpu: U9.87 (PD6); also elsewhere on the board
/Cpu/OUT4-cpu: U9.88 (PD7); also elsewhere on the board
/Cpu/OUT5-cpu: U9.61 (PD14); also elsewhere on the board
/Cpu/OUT6-cpu: U9.62 (PD15); also elsewhere on the board
/Cpu/PWM1-cpu: U9.63 (PC6); also elsewhere on the board
/Cpu/PWM2-cpu: U9.64 (PC7); also elsewhere on the board
/Cpu/PWM3-cpu: U9.65 (PC8); also elsewhere on the board
/Cpu/PWM4-cpu: U9.66 (PC9); also elsewhere on the board
/Cpu/SCK-cpu: U9.52 (PB13); also elsewhere on the board
/Cpu/SWCLK: J19.4 (SWDCLK/TCK), R85.1
/Cpu/SWDIO: J19.2 (SWDIO/TMS), R84.1
/Cpu/TRIG1-cpu: U9.89 (PB3); also elsewhere on the board
/Cpu/TRIG2-cpu: U9.47 (PB10); also elsewhere on the board
/Cpu/USB-DM: R52.1, U9.70 (PA11)
/Cpu/USB-DP: R51.1, U9.71 (PA12)
/Cpu/USB-ID: R53.1, U9.69 (PA10)
/Cpu/USB-VBUS: J18.1 (VBUS), JP3.2, R48.1
/Inputs/CS: U9.51 (PB12); also elsewhere on the board
/Inputs/MISO: U9.53 (PB14); also elsewhere on the board
/Inputs/MOSI: U9.54 (PB15); also elsewhere on the board
/Outputs/IG1: U9.81 (PD0); also elsewhere on the board
/Outputs/IG2: U9.82 (PD1); also elsewhere on the board
/Outputs/IG3: U9.83 (PD2); also elsewhere on the board
/Outputs/IG4: U9.84 (PD3); also elsewhere on the board
/Outputs/INJ1: U9.55 (PD8); also elsewhere on the board
/Outputs/INJ2: U9.56 (PD9); also elsewhere on the board
GND: C11.2, C12.2, C13.2, C14.2, C15.2, C16.2, C17.1, C18.1, C19.1, C20.1, C21.1, C22.1, C23.1, C24.1, C26.1, C27.2, C28.1, C29.2, C30.2, J16.2, J18.5 (GND), J18.6 (Shield), J19.3 (GND), J19.5 (GND), J19.9 (GNDDetect), R46.1, R49.1, U9.10 (VSS), U9.20 (VSSA), U9.27 (VSS), U9.74 (VSS), U9.99 (VSS), U10.2 (VSS), U10.8 (STBY), U11.1 (GND); also elsewhere on the board
unnamed: C11.1, U9.12 (PH0), Y1.1
unnamed: C12.1, U9.49 (VCAP_1)
unnamed: C13.1, R47.2, Y1.2
unnamed: C14.1, U9.73 (VCAP_2)
unnamed: D1.1 (K), U9.6 (VBAT)
unnamed: D1.2 (A), J16.1
unnamed: J17.1, U9.78 (PC10)
unnamed: J17.2, U9.79 (PC11)
unnamed: J17.3, U9.80 (PC12)
unnamed: J17.4, U9.7 (PC13)
unnamed: J18.2 (D-), R52.2
unnamed: J18.3 (D+), R51.2
unnamed: J18.4 (ID), R53.2
unnamed: JP1.2, R45.1
unnamed: R45.2, R46.2, U9.94 (BOOT0)
unnamed: R47.1, U9.13 (PH1)
unnamed: R48.2, U9.68 (PA9)
unnamed: R49.2, U9.37 (PB2)
unnamed: R84.2, U9.72 (PA13)
unnamed: R85.2, U9.76 (PA14)

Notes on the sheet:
Abracon ABLS 8 MHz Crystal C_L = 18 pF Pin capacitance on osc inputs = 10 pF C_L1 and C_L2 therefore are 16 pF

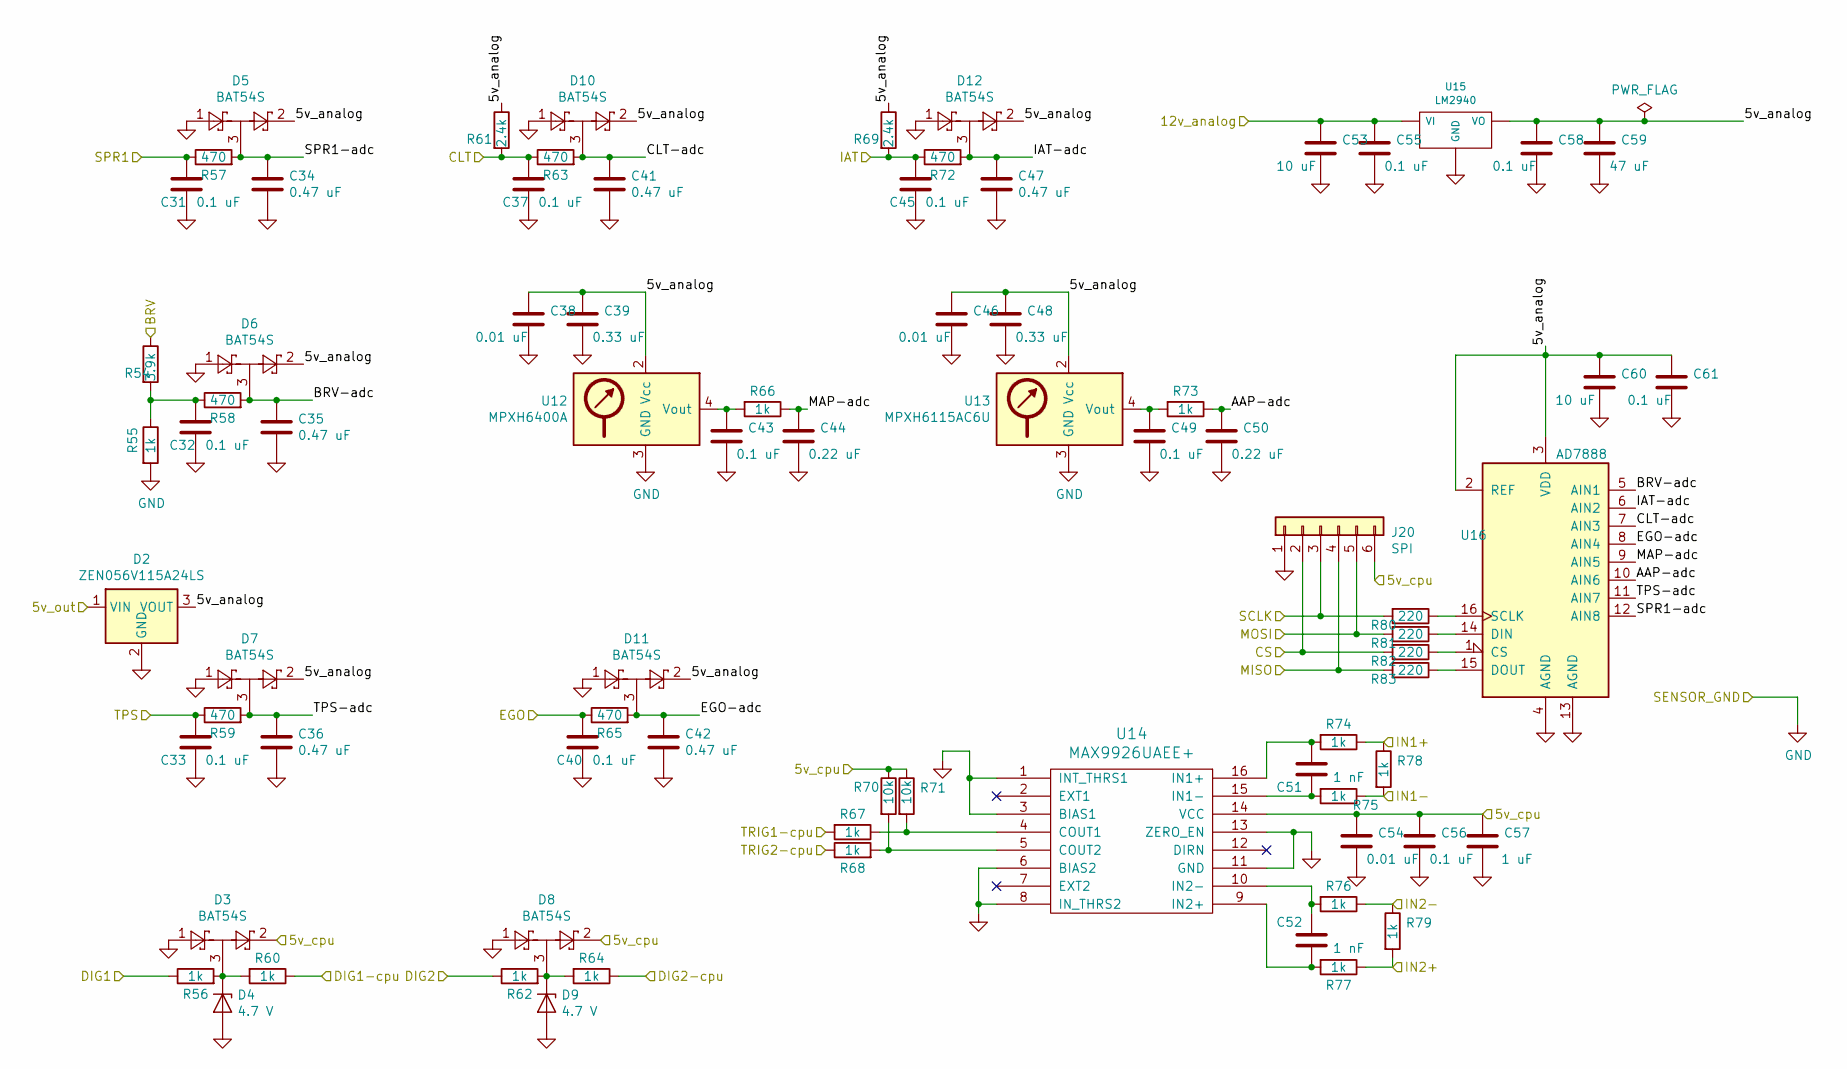
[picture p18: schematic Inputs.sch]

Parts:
C31, C32, C33, C37, C40, C45, C49, C55, C56, C58, C61: 0.1 uF; C_0805_2012Metric_Pad1.15x1.40mm_HandSolder; Digikey-Part 478-10836-1-ND
C34, C35, C36, C41, C42, C47: 0.47 uF; C_0805_2012Metric_Pad1.15x1.40mm_HandSolder; Digikey-Part 1276-6851-1-ND
C38, C46, C54: 0.01 uF; C_0805_2012Metric_Pad1.15x1.40mm_HandSolder; Digikey-Part 1276-1015-1-ND
C39, C48: 0.33 uF; C_0805_2012Metric_Pad1.15x1.40mm_HandSolder; Digikey-Part 1276-1123-1-ND
C43: 0.1 uF; C_0805_2012Metric_Pad1.15x1.40mm_HandSolder; Digikey-Part 1276-1015-1-ND
C44, C50: 0.22 uF; C_0805_2012Metric_Pad1.15x1.40mm_HandSolder; Digikey-Part 1276-1093-1-ND
C51, C52: 1 nF; C_0805_2012Metric_Pad1.15x1.40mm_HandSolder; Digikey-Part 399-1147-1-ND
C53: 10 uF; C_1206_3216Metric_Pad1.42x1.75mm_HandSolder; Digikey-Part 445-8034-1-ND
C57: 1 uF; C_0805_2012Metric_Pad1.15x1.40mm_HandSolder; Digikey-Part 1276-1066-1-ND
C59: 47 uF; C_1206_3216Metric_Pad1.42x1.75mm_HandSolder; Digikey-Part 478-9009-1-ND
C60: 10 uF; C_0805_2012Metric_Pad1.15x1.40mm_HandSolder; Digikey-Part 587-3417-1-ND
D2: ZEN056V115A24LS; Littelfuse_PolyZen-LS; Digikey-Part ZEN056V115A24LSCT-ND
D3, D5, D6, D7, D8, D10, D11, D12: BAT54S; SOT-23_Handsoldering; Digikey-Part BAT54SLT1GOSCT-ND
D4: 4.7 V; D_0603_1608Metric_Pad1.05x0.95mm_HandSolder
D9: 4.7 V; D_0805_2012Metric_Pad1.15x1.40mm_HandSolder
J20: SPI; PinHeader_1x06_P2.54mm_Vertical; Digikey-Part 732-5319-ND
R54: 3.9k; R_0805_2012Metric_Pad1.15x1.40mm_HandSolder; Digikey-Part P3.9KDACT-ND
R55: 1k; R_0805_2012Metric_Pad1.15x1.40mm_HandSolder; Digikey-Part P1.0KDACT-ND
R56, R60, R62, R64, R66, R67, R68, R73, R74, R75, R76, R77: 1k; R_0805_2012Metric_Pad1.15x1.40mm_HandSolder; Digikey-Part RNCP0805FTD1K00CT-ND
R57, R58, R59, R63, R65, R72: 470; R_0805_2012Metric_Pad1.15x1.40mm_HandSolder; Digikey-Part 311-470CRCT-ND
R61, R69: 2.4k; R_0805_2012Metric_Pad1.15x1.40mm_HandSolder; Digikey-Part P2.4KDACT-ND
R70, R71: 10k; R_0805_2012Metric_Pad1.15x1.40mm_HandSolder; Digikey-Part RNCF0805DTE10K0CT-ND
R78, R79: 1k; R_Axial_DIN0207_L6.3mm_D2.5mm_P2.54mm_Vertical; Digikey-Part PPC1.0KW-1CT-ND
R80, R81, R82, R83: 220; R_0805_2012Metric_Pad1.15x1.40mm_HandSolder; Digikey-Part A129741CT-ND
U12: MPXH6400A; Freescale_98ARH99089A; Digikey-Part MPXH6400AC6T1CT-ND
U13: MPXH6115AC6U; Freescale_98ARH99089A; Digikey-Part MPXH6115AC6U-ND
U14: MAX9926UAEE+; QSOP-16_3.9x4.9mm_P0.635mm; Digikey-Part MAX9926UAEE+TCT-ND
U15: LM2940; TO-220-3_Horizontal_TabDown; Digikey-Part LM2940T-5.0/NOPB-ND
U16: AD7888; SOIC-16_3.9x9.9mm_P1.27mm; Digikey-Part AD7888ARZ-REEL7CT-ND

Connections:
5v_cpu: C54.1, C56.1, C57.1, D3.2, D8.2, J20.6, R70.1, R71.1, U14.14 (VCC); also elsewhere on the board
/Cpu/SCK-cpu: J20.3, R80.2; also elsewhere on the board
/Cpu/TRIG1-cpu: R67.2; also elsewhere on the board
/Cpu/TRIG2-cpu: R68.1; also elsewhere on the board
/Inputs/5v_analog: C38.1, C39.1, C46.1, C48.1, C58.1, C59.1, C60.1, C61.1, D2.3 (VOUT), D5.2, D6.2, D7.2, D10.2, D11.2, D12.2, R61.1, R69.1, U12.2 (Vcc), U13.2 (Vcc), U15.3 (VO), U16.2 (REF), U16.3 (VDD)
/Inputs/5v_out: D2.1 (VIN); also elsewhere on the board
/Inputs/12v_analog: C53.1, C55.1, U15.1 (VI); also elsewhere on the board
/Inputs/AAP-adc: C50.1, R73.1, U16.10 (AIN6)
/Inputs/BRV: R54.1; also elsewhere on the board
/Inputs/BRV-adc: C35.1, D6.3, R58.2, U16.5 (AIN1)
/Inputs/CLT: C37.1, R61.2, R63.1; also elsewhere on the board
/Inputs/CLT-adc: C41.1, D10.3, R63.2, U16.7 (AIN3)
/Inputs/CS: J20.2, R82.2; also elsewhere on the board
/Inputs/DIG1: R56.1; also elsewhere on the board
/Inputs/DIG1-cpu: R60.1; also elsewhere on the board
/Inputs/DIG2: R62.1; also elsewhere on the board
/Inputs/DIG2-cpu: R64.1; also elsewhere on the board
/Inputs/EGO: C40.1, R65.1; also elsewhere on the board
/Inputs/EGO-adc: C42.1, D11.3, R65.2, U16.8 (AIN4)
/Inputs/IAT: C45.1, R69.2, R72.1; also elsewhere on the board
/Inputs/IAT-adc: C47.1, D12.3, R72.2, U16.6 (AIN2)
/Inputs/IN1+: R74.1, R78.1; also elsewhere on the board
/Inputs/IN1-: R75.1, R78.2; also elsewhere on the board
/Inputs/IN2+: R77.1, R79.2; also elsewhere on the board
/Inputs/IN2-: R76.1, R79.1; also elsewhere on the board
/Inputs/MAP-adc: C44.1, R66.1, U16.9 (AIN5)
/Inputs/MISO: J20.4, R83.2; also elsewhere on the board
/Inputs/MOSI: J20.5, R81.2; also elsewhere on the board
/Inputs/SPR1: C31.1, R57.1; also elsewhere on the board
/Inputs/SPR1-adc: C34.1, D5.3, R57.2, U16.12 (AIN8)
/Inputs/TPS: C33.1, R59.1; also elsewhere on the board
/Inputs/TPS-adc: C36.1, D7.3, R59.2, U16.11 (AIN7)
GND: C31.2, C32.2, C33.2, C34.2, C35.2, C36.2, C37.2, C38.2, C39.2, C40.2, C41.2, C42.2, C43.2, C44.2, C45.2, C46.2, C47.2, C48.2, C49.2, C50.2, C53.2, C54.2, C55.2, C56.2, C57.2, C58.2, C59.2, C60.2, C61.2, D2.2 (GND), D3.1, D4.2 (A), D5.1, D6.1, D7.1, D8.1, D9.2 (A), D10.1, D11.1, D12.1, J20.1, R55.2, U12.3 (GND), U13.3 (GND), U14.1 (INT_THRS1), U14.3 (BIAS1), U14.6 (BIAS2), U14.8 (IN_THRS2), U14.11 (GND), U14.13 (ZERO_EN), U15.2 (GND), U16.4 (AGND), U16.13 (AGND); also elsewhere on the board
unnamed: C32.1, R54.2, R55.1, R58.1
unnamed: C43.1, R66.2, U12.4 (Vout)
unnamed: C49.1, R73.2, U13.4 (Vout)
unnamed: C51.1, R74.2, U14.16 (IN1+)
unnamed: C51.2, R75.2, U14.15 (IN1-)
unnamed: C52.1, R76.2, U14.10 (IN2-)
unnamed: C52.2, R77.2, U14.9 (IN2+)
unnamed: D3.3, D4.1 (K), R56.2, R60.2
unnamed: D8.3, D9.1 (K), R62.2, R64.2
unnamed: R67.1, R71.2, U14.4 (COUT1)
unnamed: R68.2, R70.2, U14.5 (COUT2)
unnamed: R80.1, U16.16 (SCLK)
unnamed: R81.1, U16.14 (DIN)
unnamed: R82.1, U16.1 (CS)
unnamed: R83.1, U16.15 (DOUT)



Board: 2 copper layers, 136.0 x 64.0 mm, 208 parts (15 on the bottom side), 173 nets.

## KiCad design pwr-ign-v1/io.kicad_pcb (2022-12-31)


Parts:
C1: 10 uF; C_0805_2012Metric_Pad1.18x1.45mm_HandSolder; Rating Tantalum 35V
C2, C3: 0.1 uF; C_0805_2012Metric_Pad1.18x1.45mm_HandSolder; Rating X7R
C4: 1 uF; C_0805_2012Metric_Pad1.18x1.45mm_HandSolder
C5: 47 uF; C_1206_3216Metric; Rating Tantalum 10V
C6, C7: 1n; C_0805_2012Metric_Pad1.18x1.45mm_HandSolder
C8: 10n; C_0805_2012Metric_Pad1.18x1.45mm_HandSolder
C9: 0.1u; C_0805_2012Metric_Pad1.18x1.45mm_HandSolder
C10: 1u; C_0805_2012Metric_Pad1.18x1.45mm_HandSolder
D1, D2, D5, D6, D7, D8, D9: LED; LED_0805_2012Metric_Pad1.15x1.40mm_HandSolder
D3, D4: BAT54S; SOT-23
J1: DIG-in; PinHeader_1x02_P2.54mm_Vertical
JP1: IG_PWR; SolderJumper-3_P1.3mm_Open_Pad1.0x1.5mm
P1: IN-CPU; PinHeader_1x04_P2.54mm_Vertical
P2: TRIG-cpu; PinHeader_1x04_P2.54mm_Vertical
P3: DIG-CPU; PinHeader_1x04_P2.54mm_Vertical
P4: CPU_PWR; PinHeader_1x04_P2.54mm_Vertical
P5: IGNITION; PinHeader_1x04_P2.54mm_Vertical
P6: TRIG-IN; PinHeader_1x04_P2.54mm_Vertical
P7: PWR_IN; PinHeader_1x04_P2.54mm_Vertical
R1, R2, R3, R4, R5, R10, R14, R16, R17, R18, R19, R20, R21, R22, R23, R24, R25, R26: 1k; R_0805_2012Metric_Pad1.20x1.40mm_HandSolder
R6, R8, R33: 2.4k; R_0805_2012Metric_Pad1.20x1.40mm_HandSolder
R7, R11, R13, R15: 100k; R_0805_2012Metric_Pad1.20x1.40mm_HandSolder
R9, R12: 10k; R_0805_2012Metric_Pad1.20x1.40mm_HandSolder
R27, R28, R29, R30: 150; R_0805_2012Metric_Pad1.20x1.40mm_HandSolder
R31, R32: 330; R_Axial_DIN0207_L6.3mm_D2.5mm_P2.54mm_Vertical
U1: LM2940; TO-220-3_Horizontal_TabDown
U2: MIC4469; SOIC-16W_7.5x10.3mm_P1.27mm
U3: MAX9926UAEE+; QSOP-16_3.9x4.9mm_P0.635mm

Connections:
5v: C3.1, C5.1, C8.1, C9.1, C10.1, D1.2 (A), D2.2 (A), D3.2, D4.2, JP1.3 (B), P2.1, P3.4, P4.1, P4.2, R9.1, R12.1, R33.1, U1.3 (VO), U3.14 (VCC)
12v_power: C1.1, C2.1, JP1.1 (A), P7.1, P7.2, U1.1 (VI)
DIG1-cpu: P3.2, R10.2
DIG1-in: J1.1, R14.1
DIG2-cpu: P3.3, R16.2
DIG2-in: J1.2, R19.1
GND: C1.2, C2.2, C3.2, C4.2, C5.2, C8.2, C9.2, C10.2, D3.1, D4.1, D5.1 (K), D6.1 (K), D7.1 (K), D8.1 (K), D9.1 (K), P2.4, P3.1, P4.3, P4.4, P7.3, P7.4, R7.1, R11.1, R13.1, R15.1, U1.2 (GND), U2.2 (1B), U2.4 (2B), U2.6 (3B), U2.7 (GND), U2.8 (GND), U2.10 (4B), U3.1 (INT_THRS1), U3.3 (BIAS1), U3.6 (BIAS2), U3.8 (IN_THRS2), U3.11 (GND), U3.13 (ZERO_EN)
IG1-cpu: P1.1, R3.2
IG1-out: P5.1, R27.1
IG2-cpu: P1.2, R4.2
IG2-out: P5.2, R28.1
IG3-cpu: P1.3, R5.2
IG3-out: P5.3, R29.1
IG4-cpu: P1.4, R17.2
IG4-out: P5.4, R30.1
unnamed: C4.1, JP1.2 (C), U2.15 (Vs), U2.16 (Vs)
unnamed: C6.1, R23.2, U3.16 (IN1+)
unnamed: C6.2, R24.2, U3.15 (IN1-)
unnamed: C7.1, R25.2, U3.10 (IN2-)
unnamed: C7.2, R26.2, U3.9 (IN2+)
unnamed: D1.1 (K), R6.1
unnamed: D2.1 (K), R8.1
unnamed: D3.3, R10.1, R14.2
unnamed: D4.3, R16.1, R19.2
unnamed: D5.2 (A), R18.1
unnamed: D6.2 (A), R20.1
unnamed: D7.2 (A), R21.1
unnamed: D8.2 (A), R22.1
unnamed: D9.2 (A), R33.2
unnamed: R1.1, R8.2, R12.2, U3.4 (COUT1)
unnamed: R2.1, R6.2, R9.2, U3.5 (COUT2)
unnamed: R5.1, R7.2, U2.5 (3A)
unnamed: R4.1, R11.2, U2.3 (2A)
unnamed: R3.1, R13.2, U2.1 (1A)
unnamed: R15.2, R17.1, U2.9 (4A)
unnamed: R18.2, R27.2, U2.14 (1Y)
unnamed: R20.2, R28.2, U2.13 (2Y)
unnamed: R21.2, R29.2, U2.12 (3Y)
unnamed: R22.2, R30.2, U2.11 (4Y)
TRIG1: P2.3, R1.2
TRIG1IN+: P6.2, R23.1, R31.1
TRIG1IN-: P6.1, R24.1, R31.2
TRIG2: P2.2, R2.2
TRIG2IN+: P6.4, R26.1, R32.2
TRIG2IN-: P6.3, R25.1, R32.1

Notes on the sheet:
Power Supplies
Ignition Drivers
Trigger Inputs
Digital Inputs


Board: 2 copper layers, 77.8 x 33.9 mm, 64 parts (0 on the bottom side), 45 nets.

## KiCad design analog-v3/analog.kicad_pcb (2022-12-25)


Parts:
C1: 10 uF; C_0805_2012Metric_Pad1.18x1.45mm_HandSolder; Rating 35V Tantalum
C2, C21, C22, C26, C29: 0.47 uF; C_0805_2012Metric_Pad1.18x1.45mm_HandSolder
C3, C5, C6, C9, C10, C12, C13, C17, C25: 0.1 uF; C_0805_2012Metric_Pad1.18x1.45mm_HandSolder
C4, C7, C11, C15, C16, C19: 1 uF; C_0805_2012Metric_Pad1.18x1.45mm_HandSolder
C8: 47 uF; C_1206_3216Metric_Pad1.33x1.80mm_HandSolder; Rating 10 V Tantalum
C20: 0.01 uF; C_0805_2012Metric_Pad1.18x1.45mm_HandSolder
C24: 0.33 uF; C_0805_2012Metric_Pad1.18x1.45mm_HandSolder
D1, D2, D3, D6, D8, D9, D10, D12: BAT54S; SOT-23
D4: 5.4 V; D_A-405_P2.54mm_Vertical_AnodeUp
D5: LED; LED_0805_2012Metric_Pad1.15x1.40mm_HandSolder
F1: 500 mA; Fuse_1206_3216Metric_Pad1.42x1.75mm_HandSolder
H1, H2, H3, H4: MountingHole_Pad; MountingHole_3mm_Pad
J1: SPARE; PinHeader_1x04_P2.54mm_Vertical
J2: Inputs; PinHeader_1x08_P2.54mm_Vertical
J5: POWER; PinHeader_1x04_P2.54mm_Vertical
P1: SPI; PinHeader_1x06_P2.54mm_Vertical
P2: DEBUG; PinHeader_1x06_P2.54mm_Vertical
R1, R3, R5, R11, R27, R28, R29, R31, R34: 220; R_0805_2012Metric_Pad1.20x1.40mm_HandSolder
R2, R4: 2.49k; R_0805_2012Metric_Pad1.20x1.40mm_HandSolder; Rating 0.1%
R6, R7, R22, R23: 1000; R_0805_2012Metric_Pad1.20x1.40mm_HandSolder
R8, R9: 330; R_0805_2012Metric_Pad1.20x1.40mm_HandSolder
R10: 2.4k; R_0805_2012Metric_Pad1.20x1.40mm_HandSolder
R12, R13: 120; R_0805_2012Metric_Pad1.20x1.40mm_HandSolder
R16: 100; R_0805_2012Metric_Pad1.20x1.40mm_HandSolder
R18, R19, R20, R21: 10k; R_0805_2012Metric_Pad1.20x1.40mm_HandSolder
R25: 3.9k; R_0805_2012Metric_Pad1.20x1.40mm_HandSolder; Rating 0.1%
R26: 1k; R_0805_2012Metric_Pad1.20x1.40mm_HandSolder; Rating 0.1%
TP1: EOC; TestPoint_THTPad_1.0x1.0mm_Drill0.5mm
TP2: KNK1; TestPoint_THTPad_1.0x1.0mm_Drill0.5mm
TP3: KNK2; TestPoint_THTPad_1.0x1.0mm_Drill0.5mm
U1: TLV2553; SOIC-20W_7.5x12.8mm_P1.27mm
U2: LM2940; TO-220-3_Horizontal_TabDown
U3: MCP6002-xSN; MSOP-8_3x3mm_P0.65mm
U4: MPXA6400A; Freescale_98ARH99089A

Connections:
2v5_knock: R22.2, R23.1, U3.3 (+), U3.5 (+)
5v_analog: C5.1, C6.1, C7.1, C8.1, C16.1, C17.1, C20.1, C24.1, D1.2, D2.2, D3.2, D4.1 (K), D6.2, D8.2, D9.2, D10.2, D12.2, F1.2, P1.1, P2.1, R2.1, R4.1, R10.1, R18.1, R19.1, R20.1, R21.1, R22.1, U1.14 (REF+), U1.20 (VCC), U2.3 (VO), U3.8 (V+), U4.2 (Vcc)
5v_out: F1.1, J5.3
12v_analog: C1.1, C3.1, J5.4, R25.1, U2.1 (VI)
ADC_CLK: P1.2, P2.2, R19.2, U1.18 (I/O_CLOCK)
ADC_CS: P1.5, P2.5, R18.2, U1.15 (~CS)
ADC_MISO: R16.2, U1.16 (DATA_OUT)
ADC_MOSI: P1.3, P2.3, R20.2, U1.17 (DATA_INPUT)
BRV-adc: C19.1, D8.3, R27.1, U1.3 (AIN2)
CLT-adc: C4.1, D2.3, R3.1, U1.6 (AIN5)
CLT-in: J2.5, R2.2, R3.2
EGO-adc: C2.1, D1.3, R1.1, U1.8 (AIN7)
EGO-in: J2.3, R1.2
GND: C1.2, C2.2, C3.2, C4.2, C5.2, C6.2, C7.2, C8.2, C11.2, C12.2, C13.2, C15.2, C16.2, C17.2, C19.2, C20.2, C21.2, C22.2, C24.2, C25.2, C26.2, C29.2, D1.1, D2.1, D3.1, D4.2 (A), D5.1 (K), D6.1, D8.1, D9.1, D10.1, D12.1, J1.1, J2.1, J2.2, J5.1, J5.2, P1.6, P2.6, R23.2, R26.2, U1.10 (GND), U1.13 (REF-), U2.2 (GND), U3.4 (V-), U4.3 (GND)
IAT-adc: C11.1, D3.3, R5.1, U1.5 (AIN4)
IAT-in: J2.6, R4.2, R5.2
KNK1: C9.2, J2.7
KNK1-adc: C12.1, R12.1, TP2.1, U1.1 (AIN0)
KNK2: C10.2, J2.8
KNK2-adc: C13.1, R13.1, TP3.1, U1.2 (AIN1)
MAP-adc: C29.1, R34.1, U1.4 (AIN3)
unnamed: C9.1, R6.2
unnamed: C10.1, R7.2
unnamed: C25.1, R34.2, U4.4 (Vout)
unnamed: D5.2 (A), R10.2
unnamed: P1.4, P2.4, R16.1, R21.2
unnamed: R6.1, R8.2, U3.2 (-)
unnamed: R7.1, R9.2, U3.6 (-)
unnamed: R8.1, R12.2, U3.1
unnamed: R9.1, R13.2, U3.7
unnamed: R25.2, R26.1, R27.2
unnamed: TP1.1, U1.19 (EOC)
SPR1-adc: C21.1, D9.3, R28.1, U1.9 (AIN8)
SPR1-in: J1.2, R28.2
SPR2-adc: C26.1, D12.3, R31.1, U1.11 (AIN9)
SPR2-in: J1.3, R31.2
SPR3-adc: C22.1, D10.3, R29.1, U1.12 (AIN10)
SPR3-in: J1.4, R29.2
TPS-adc: C15.1, D6.3, R11.1, U1.7 (AIN6)
TPS-in: J2.4, R11.2



Board: 2 copper layers, 77.8 x 33.9 mm, 78 parts (6 on the bottom side), 40 nets.

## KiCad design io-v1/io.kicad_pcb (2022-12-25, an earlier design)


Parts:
C1, C2: 0.1 uF; C_Disc_D3_P2.5
C3, C4, C5: 1 uF; C_Disc_D3_P2.5
C6: 10 uF; C_Disc_D3_P2.5; Rating Tantalum 35V
C7, C8: 0.1 uF; C_Disc_D3_P2.5; Rating X7R
C9: 47 uF; C_Disc_D3_P2.5; Rating Tantalum 10V
D1: 3.3 V Zener; Diode_DO-41_SOD81_Vertical_KathodeUp
D2, D3, D11, D12, D20, D21, D22, D23, D24, D25, D26, D27: D; Diode_DO-41_SOD81_Vertical_KathodeUp
D4, D19: D_Zener; Diode_DO-41_SOD81_Vertical_KathodeUp
D5, D6, D7, D8, D9, D10, D13, D14, D15, D16, D17, D18: LED; LED-3MM
P1, P2, P3: CONN_01X04; Pin_Header_Straight_1x04
P4: CONN_02X06; Pin_Header_Straight_2x06
P5: CONN_02X09; Pin_Header_Straight_2x09
Q1, Q2, Q3, Q4, Q5, Q6: VND7NV04; TO-252-2Lead
R1, R2, R3, R4, R5, R6, R7, R14, R21, R29, R48: 1k; Resistor_Horizontal_RM7mm
R8, R9, R10, R11, R12, R13, R34, R35, R36, R37, R40, R41: 100k; Resistor_Horizontal_RM7mm
R17, R18, R19, R20: 150; Resistor_Horizontal_RM7mm
R22, R23, R25, R26, R27, R28, R30, R31, R32, R33, R38, R39: 2.43k; Resistor_Horizontal_RM7mm
R24: 120; Resistor_Horizontal_RM7mm
R42, R43, R44, R45, R46, R47: 330; Resistor_Horizontal_RM7mm
U1: TC4424; DIP-8_W7.62mm
U2, U3: TC4427; DIP-8_W7.62mm
U4: MCP2562-H/P; DIP-8_W7.62mm
U5: LM2940; TO-220_Neutral123_Horizontal_LargePads

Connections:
5v_cpu: C2.2, C8.1, C9.1, D2.1 (K), D11.1 (K), P5.2, R1.1, U4.3 (VDD), U5.3 (VO)
12v_power: C3.1, C4.1, C5.1, C6.1, C7.1, P4.1, R30.2, R31.2, R32.2, R33.2, R38.2, R39.2, U1.6 (VDD), U2.6 (VDD), U3.6 (VDD), U5.1 (VI)
CAN_H: P4.11, R24.1, U4.7 (CANH)
CAN_L: P4.12, R24.2, U4.6 (CANL)
CAN_RX: P5.18, U4.4 (RXD)
CAN_TX: P5.17, U4.1 (TXD)
DIG1-cpu: P5.15, R14.2
DIG1-in: P4.7, R21.1
DIG2-cpu: P5.16, R29.2
DIG2-in: P4.9, R48.1
GND: C1.2, C2.1, C3.2, C4.2, C5.2, C6.2, C7.2, C8.2, C9.2, D1.2 (A), D3.2 (A), D4.2 (A), D5.1 (K), D6.1 (K), D7.1 (K), D8.1 (K), D9.1 (K), D10.1 (K), D12.2 (A), D19.2 (A), P4.2, P5.1, R8.1, R9.2, R10.1, R11.2, R12.1, R13.2, R34.2, R35.2, R36.2, R37.2, R40.2, R41.2, U1.3 (GND), U2.3 (GND), U3.3 (GND), U4.2 (VSS), U4.8 (STBY), U5.2 (GND)
HSD1-cpu: P5.13, R2.2
HSD1-out: D26.2 (A), P4.10, U1.7 (OUTA)
HSD2-cpu: P5.14, R3.2
HSD2-out: D27.2 (A), P4.8, U1.5 (OUTB)
IG1-cpu: P5.11, R4.2
IG1-out: P4.5, R17.1, R25.1
IG2-cpu: P5.12, R5.2
IG2-out: P4.6, R18.1, R26.1
IG3-cpu: P5.9, R6.2
IG3-out: P4.3, R19.1, R27.1
IG4-cpu: P5.10, R7.2
IG4-out: P4.4, R20.1, R28.1
INJ1-cpu: P5.5, R34.1, R42.2
INJ1-out: D20.1 (K), P2.1, Q1.2 (D)
INJ2-cpu: P5.6, R35.1, R43.2
INJ2-out: D21.1 (K), P2.3, Q2.2 (D)
INJ3-cpu: P5.3, R36.1, R44.2
INJ3-out: D22.1 (K), P3.1, Q3.2 (D)
INJ4-cpu: P5.4, R37.1, R45.2
INJ4-out: D23.1 (K), P3.3, Q4.2 (D)
LSD1-cpu: P5.7, R40.1, R46.2
LSD1-out: D24.1 (K), P1.1, Q5.2 (D)
LSD2-cpu: P5.8, R41.1, R47.2
LSD2-out: D25.1 (K), P1.3, Q6.2 (D)
unnamed: C1.1, D1.1 (K), R1.2, U4.5 (Vio)
unnamed: D2.2 (A), D3.1 (K), D4.1 (K), R14.1, R21.2
unnamed: D5.2 (A), R22.1
unnamed: D6.2 (A), R23.2
unnamed: D7.2 (A), R25.2
unnamed: D8.2 (A), R26.2
unnamed: D9.2 (A), R27.2
unnamed: D10.2 (A), R28.2
unnamed: D11.2 (A), D12.1 (K), D19.1 (K), R29.1, R48.2
unnamed: D13.1 (K), D20.2 (A)
unnamed: D13.2 (A), R30.1
unnamed: D14.1 (K), D21.2 (A)
unnamed: D14.2 (A), R31.1
unnamed: D15.1 (K), D22.2 (A)
unnamed: D15.2 (A), R32.1
unnamed: D16.1 (K), D23.2 (A)
unnamed: D16.2 (A), R33.1
unnamed: D17.1 (K), D24.2 (A)
unnamed: D17.2 (A), R38.1
unnamed: D18.1 (K), D25.2 (A)
unnamed: D18.2 (A), R39.1
unnamed: D26.1 (K), R22.2
unnamed: D27.1 (K), R23.1
unnamed: Q1.1 (G), R42.1
unnamed: Q2.1 (G), R43.1
unnamed: Q3.1 (G), R44.1
unnamed: Q4.1 (G), R45.1
unnamed: Q5.1 (G), R46.1
unnamed: Q6.1 (G), R47.1
unnamed: R2.1, R8.2, U1.2 (INA)
unnamed: R3.1, R9.1, U1.4 (INB)
unnamed: R4.1, R10.2, U2.2 (INA)
unnamed: R5.1, R11.1, U2.4 (INB)
unnamed: R6.1, R12.2, U3.2 (INA)
unnamed: R7.1, R13.1, U3.4 (INB)
unnamed: R17.2, U2.7 (OUTA)
unnamed: R18.2, U2.5 (OUTB)
unnamed: R19.2, U3.7 (OUTA)
unnamed: R20.2, U3.5 (OUTB)
OUT_GND: P1.2, P1.4, P2.2, P2.4, P3.2, P3.4, Q1.3 (S), Q2.3 (S), Q3.3 (S), Q4.3 (S), Q5.3 (S), Q6.3 (S)

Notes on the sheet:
Power Supplies
Injector Drivers
Ignition Drivers
High-Side Drivers
Low-Side Drivers
CANBUS
Digital Inputs


Board: 2 copper layers, 107.0 x 58.0 mm, 98 parts (0 on the bottom side), 75 nets.

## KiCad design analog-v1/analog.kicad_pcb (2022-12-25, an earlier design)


Board: 2 copper layers, 80.0 x 40.0 mm, 63 parts (0 on the bottom side), 30 nets.

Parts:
C1, C18, C20: 10 uF; C_Disc_D3_P2.5
C2, C3, C4, C7, C9, C10, C13, C14, C15, C19: 0.1 uF; C_Disc_D3_P2.5
C5, C6, C11, C12, C16, C17, C21, C22, C23, C24, C25: 0.47 uF; C_Disc_D3_P2.5
C8: 47 uF; C_Disc_D3_P2.5
D1, D2, D3, D4, D5, D6, D7, D8, D9, D10, D11, D12: 1N5818; Diode_DO-41_SOD81_Vertical_KathodeUp
P1: CONN_01X09; Pin_Header_Straight_1x09
P2, P3: CONN_01X06; Pin_Header_Straight_1x06
P4: CONN_01X05; Pin_Header_Straight_1x05
R1, R4, R9: 2.49k; Resistor_Horizontal_RM7mm
R2, R3, R5, R6, R10, R11: 470; Resistor_Horizontal_RM7mm
R7: 3.9k; Resistor_Horizontal_RM7mm
R8: 1k; Resistor_Horizontal_RM7mm
R12, R13, R14, R15, R16: 100; Resistor_Horizontal_RM7mm
R17, R18, R19, R20: 10k; Resistor_Horizontal_RM7mm
U1: LM2940; TO-220_Neutral123_Horizontal
U2: TLC2543; DIP-20_W7.62mm

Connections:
5v_analog: C7.1, C8.1, C15.1, C18.1, C19.1, C20.1, D1.1, D3.1, D5.1, D7.1, D9.1, D11.1, P1.3, R1.1, R4.1, R9.1, R17.1, R18.1, R19.1, R20.1, U1.3, U2.14, U2.20
12v_analog: C1.1, C4.1, P1.1, R7.1, U1.1
ADC_CLK: R13.2, U2.18
ADC_CS: R16.2, U2.15
ADC_EOC: R12.2, U2.19
ADC_MISO: R15.2, U2.16
ADC_MOSI: R14.2, U2.17
BRV-adc: C17.1, D11.2, D12.1, R11.1, U2.1
CLT-adc: C5.1, D1.2, D2.1, R2.1, U2.3
CLT-in: C2.1, P1.5, R1.2, R2.2
EGO-adc: C12.1, D7.2, D8.1, R6.1, U2.5
EGO-in: C10.1, P1.7, R6.2
EX-1: C21.1, P4.1, U2.7
EX-2: C22.1, P4.2, U2.8
EX-3: C23.1, P4.3, U2.9
EX-4: C24.1, P4.4, U2.11
EX-5: C25.1, P4.5, U2.12
GND: C1.2, C2.2, C3.2, C4.2, C5.2, C6.2, C7.2, C8.2, C9.2, C10.2, C11.2, C12.2, C13.2, C14.2, C15.2, C16.2, C17.2, C18.2, C19.2, C20.2, C21.2, C22.2, C23.2, C24.2, C25.2, D2.2, D4.2, D6.2, D8.2, D10.2, D12.2, P1.2, P1.9, P2.6, P3.6, R8.2, U1.2, U2.10, U2.13
IAT-adc: C11.1, D5.2, D6.1, R5.1, U2.2
IAT-in: C9.1, P1.4, R4.2, R5.2
unnamed: C14.1, R7.2, R8.1, R11.2
unnamed: P2.1, P3.1, R12.1
unnamed: P2.2, P3.2, R13.1, R20.2
unnamed: P2.3, P3.3, R14.1, R19.2
unnamed: P2.4, P3.4, R15.1, R18.2
unnamed: P2.5, P3.5, R16.1, R17.2
SPR-adc: C16.1, D9.2, D10.1, R10.1, U2.6
SPR-in: C13.1, P1.8, R9.2, R10.2
TPS-adc: C6.1, D3.2, D4.1, R3.1, U2.4
TPS-in: C3.1, P1.6, R3.2

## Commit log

2020-12-18 Add prototyping board based on stm32f427
    [proto-stm32f427.kicad_pcb, proto-stm32f427.sch, proto-stm32f427_bom_.csv]
2022-12-25 Add various other experimental boards.
    IO V1 and Analog V1 are the original testing boards, all throughhole. The
    analog board uses a tlc2543 and still would work, but the IO board needs
    proper gate drivers to have acceptable FET speeds. Analog V2 uses a max11632
    which may or may not be a failed experiment. IO v2 adds trigger input
    handling, and uses mic4469's to drive FETs, and is usable except its a bit
    too big for my needs.
    [analog.kicad_pcb, analog.kicad_sch, analog.sch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]
2022-12-25 analog-v3, now with a tlc2553, two knock sensor inputs, all the cores, and 3 spares
    [analog.kicad_pcb, analog.sch]
2022-12-31 Rework IO board to just be an LSD breakout board
    [io.kicad_pcb, io.kicad_sch, io.sch]
2022-12-31 Add new IO board without LSD's, just 4x ignition, 2x VR, 2x digital input, and a 5v supply
    [io-B_Cu.gbl, io-B_Mask.gbs, io-B_Silkscreen.gbo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]
2022-12-31 Add old Viaems board
    [Inputs.sch, Outputs.sch, cpu.sch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]
2023-05-16 New improved core board for stm32f427
    [proto-stm32f427-B_Cu.gbl, proto-stm32f427-B_Mask.gbs, proto-stm32f427-B_Paste.gbp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]
2026-05-08 Implement an MCXE24x LQFP64 core board.
    [proto-mcxe246.kicad_pcb, proto-mcxe246.kicad_sch]
2026-05-10 MCXC244 Prototyping board
    Intended for USB/UART comms
    [mcxc244-usb.kicad_pcb, mcxc244-usb.kicad_sch]
